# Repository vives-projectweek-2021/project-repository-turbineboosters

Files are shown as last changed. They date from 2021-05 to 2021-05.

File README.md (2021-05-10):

# TurbineBoosters
Welcome to our project repository!

## Choice of motor

To create our windturbine we had to make some choices. The first choice we had to make was wich motor to use as generator.
It soon became clear to us that we had to use a 3 phasse BLDC motor.
We looked around at our options and had 2 motors available, one that generates around 60V:

afbeelding

and another one that generates only around 6V, but has more power:

afbeelding

We decided to go for the motor that generates 60V because we lose 1,4V across the diodes of our 3 phase bridge rectifier and that leaves us with an efficiency of 96%, while the other motor would only offer us an efficiency of about 77%.

## Rectifier + first LoRa module

The power generated by our motor is fed to a 3 phase bridge rectifier.
On this board we measure the current and voltage via a shunt-resistor of 0,5Ω.
The LoRa module (RN2483A) receives this data and sends it peer-to-peer to another LoRa module:

afbeelding

## Lorawan receiver 

The data that we recieve over lorawan on the SODAQ Explorer microconroller is than formated to a byte array. Then the data is send over bluetooth and send to a raspberry pi.

First we wanted to send the data over bluetooth low energy that was on the controller. But the bleutooth HC05 chip doesn't take that much power and is easier to use. 

afbeelding

## Raspberry pi

The data that we receive over bluetooth is than but into an influxdb database. This data is than visualized with the use of grafana.

afbeelding

## Mechanical design

afbeelding

We mounted a bicycle wheel on the shaft of our motor, to which we attached 8 PVC-blades via 3D-printed coupling pieces.

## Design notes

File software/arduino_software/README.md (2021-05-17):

# RN2483_PeerToPeer
 
 This is an example on how to use the RN2483 LoRaWan modem to acheive a secure peer to peer communication.
 
 This library is made for those who have a RN2483 on an existing board. Microchip doesn't advertise the use of peer to peer communication with their RN2483 chips because they were specifically desgined for the LoRaWAN protocol stack. If you are a developer who wants to implement peer to peer communication it is recomended that you directly use the SX12xx lora modems from the start.
 
 This library exploits the limited peer to peer possibilities of the RN2483 to implement secure communication with another RN2483. The connection is stateless so you can broadcast a packet and the device with the correct key and adress will decode and handle the packet.
 
 This library is still in early development. Feel free to add issues or create pull requests if you want to see features added.
 
 planned features:
 * CRC
 * Handshaking
 * Compatibility with other lora modems
 * replay attack prevention
 
 Here is an example sketch:
 
 ```C++
#include "RN2483_P2P.h"

#define loraSerial              Serial2
#define usbSerial               SerialUSB

// Both devices mush have the same AES-key.
const byte key[16] = {0x00, 0x01, 0x02, 0x03, 0x04, 0x05, 0x06, 0x07, 0x08, 0x09, 0x0A, 0x0B, 0x0C, 0x0D, 0x0E, 0x0F};

// set the address of the device where you want te send a packet to
const byte targetAddress[1] = {0x00};

// the adress of this device (The adresses can be the same. It won't loop back)
const byte deviceAddress[1] = {0x00};

RN2483_P2P peerToPeer(usbSerial, loraSerial);

void setup() {

    usbSerial.begin(115200);
    loraSerial.begin(57600);
    loraSerial.setTimeout(1000);
    lora_autobaud();

    usbSerial.println("initializing...");
    
    peerToPeer.initLoRa();
    peerToPeer.setAesKey(key);
    peerToPeer.setAddress(deviceAddress);
}

void loop() 
{
    // uncomment for the transmitter
    //byte payload[10] = {0, 1, 2, 3, 4, 5, 6, 7, 8, 9};
    //peerToPeer.transmitMessage(payload, targetAddress);

    // uncomment for the receiver
    peerToPeer.receiveMessage(handleMessage);
}

void handleMessage(const byte *payload)
{
    // handle the received payload
    
    for (int i=0; i < 10; i++){
        usbSerial.println( (int) payload[i] );
    }
}

void lora_autobaud()
{
    String response = "";
    while (response=="")
    {
        delay(1000);
        loraSerial.write((byte)0x00);
        loraSerial.write(0x55);
        loraSerial.println();
        loraSerial.println("sys get ver");
        response = loraSerial.readStringUntil('\n');
    }
}
 ```
 The code where this library is build upon is [this Code ecample.](https://github.com/jpmeijers/RN2483-Arduino-p2p-examples) <br>
 The encryption library used is [this AES library.](https://github.com/bigfighter/arduino-AES)
 
 This code was tested on a SODAQ ExpLoRer withe an RN2483A with firmware version 1.0.4 but should work on all boards with the RN2483.

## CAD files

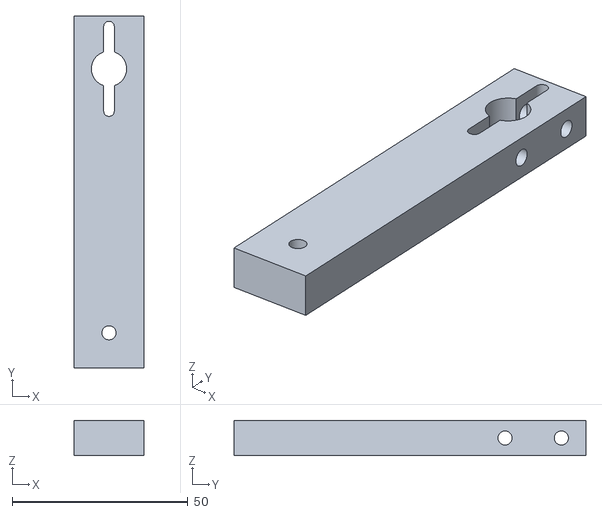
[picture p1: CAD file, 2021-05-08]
hardware/3D_prints/handle.stl
20.0 x 100.0 x 10.0

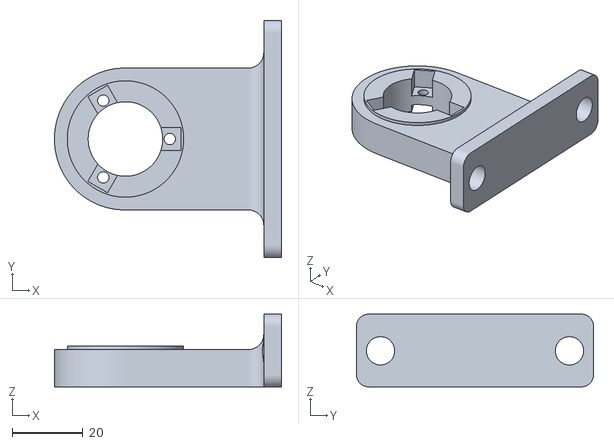
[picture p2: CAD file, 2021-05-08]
hardware/3D_prints/generator_mount.stl
64.0 x 66.9 x 20.5

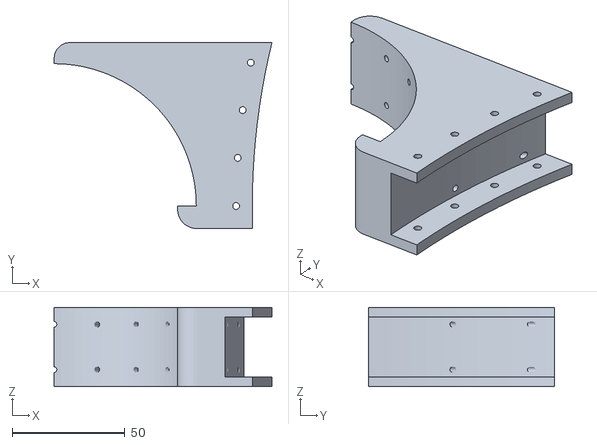
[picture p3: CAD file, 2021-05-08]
hardware/3D_prints/wiek_houder.stl
96.5 x 82.4 x 35.0

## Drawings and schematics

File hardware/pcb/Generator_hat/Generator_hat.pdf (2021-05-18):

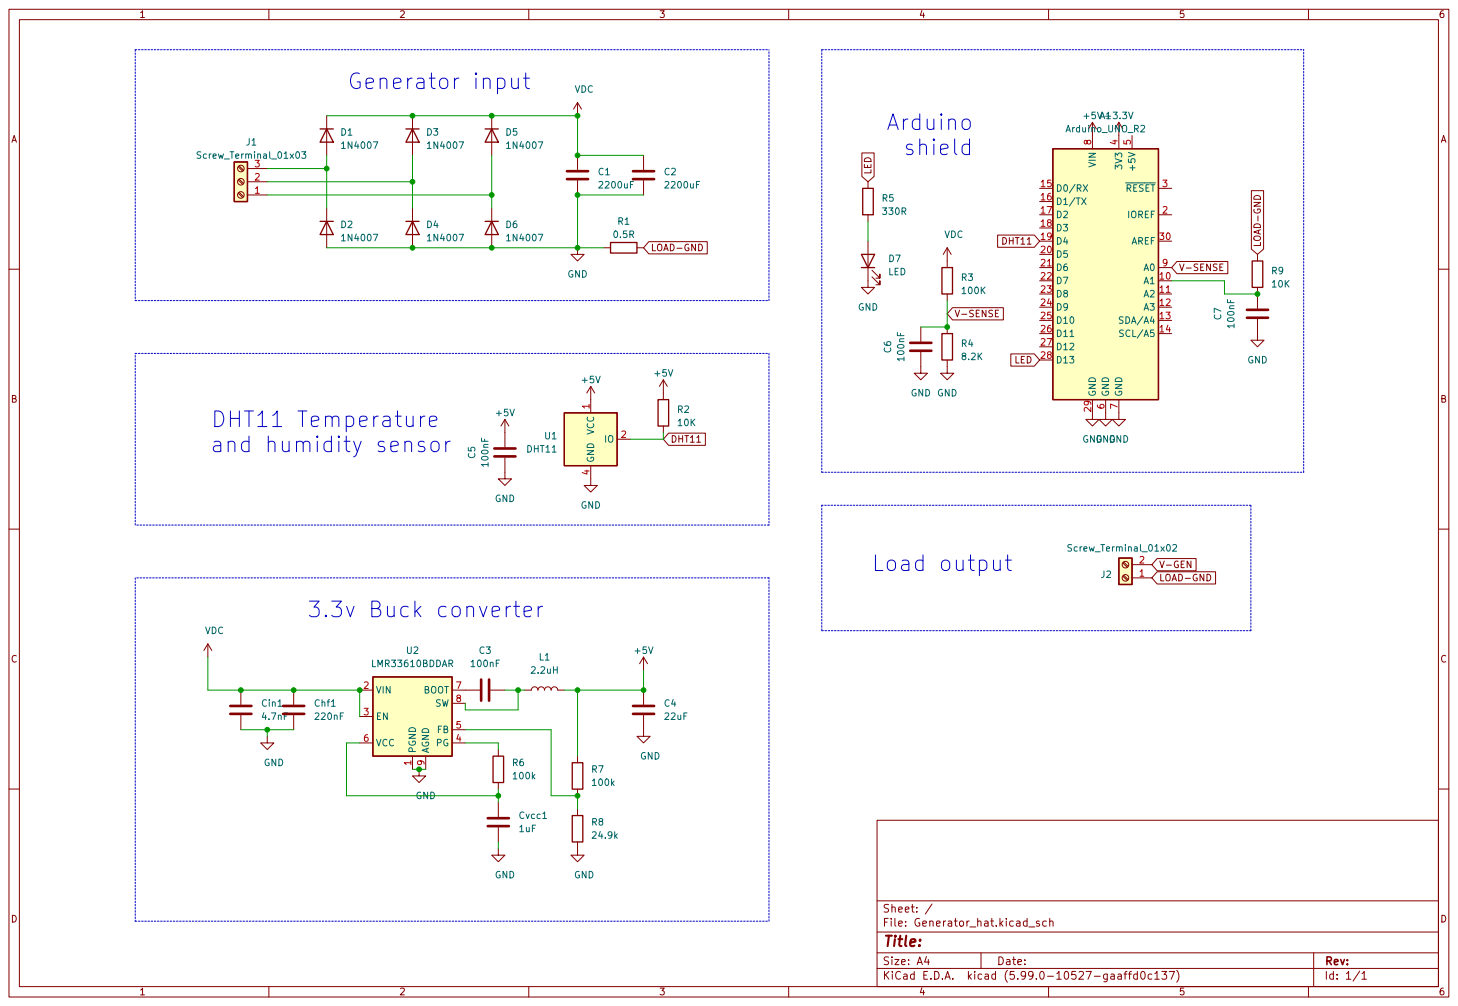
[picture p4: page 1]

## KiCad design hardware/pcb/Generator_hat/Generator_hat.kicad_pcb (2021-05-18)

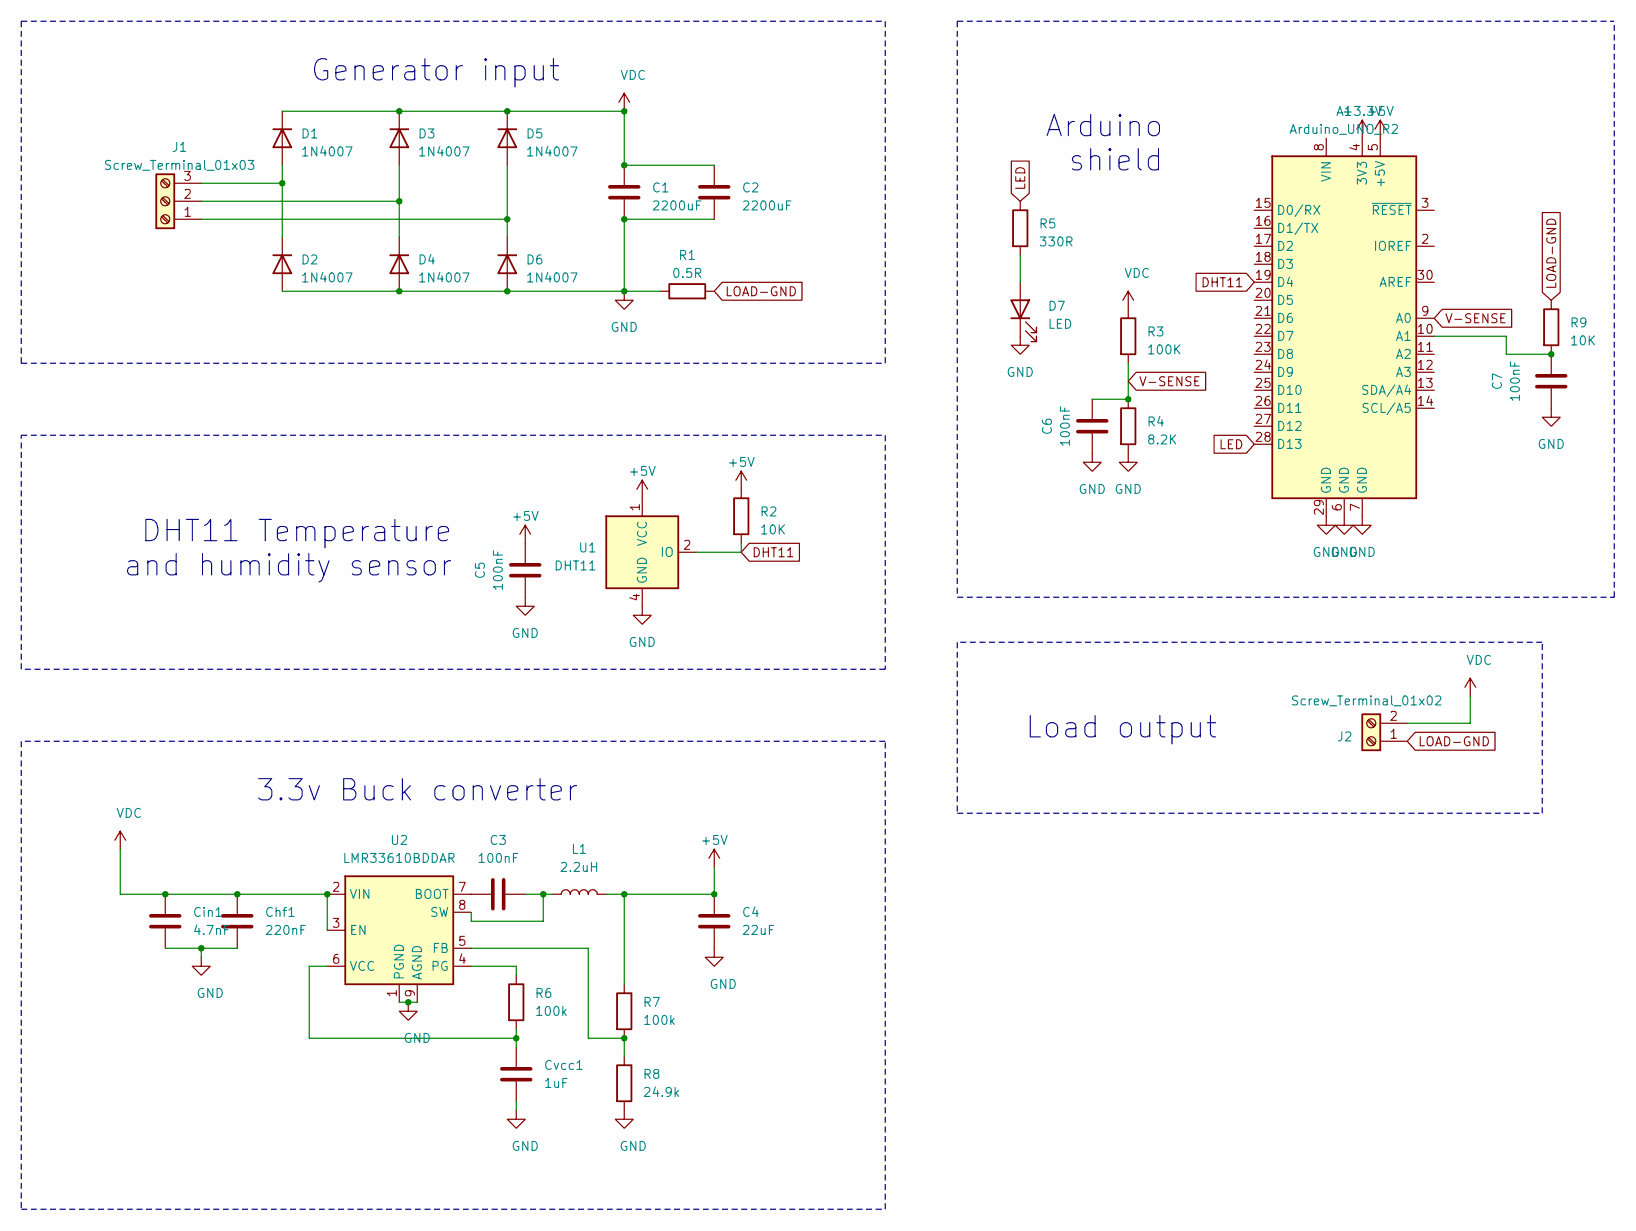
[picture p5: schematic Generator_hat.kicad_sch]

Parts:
A1: Arduino_UNO_R2
C1, C2: 2200uF; CP_Radial_D16.0mm_P7.50mm
C3, C5, C6, C7: 100nF; C_0805_2012Metric_Pad1.18x1.45mm_HandSolder
C4: 22uF; CP_Elec_8x6.9
Chf1: 220nF; C_0805_2012Metric_Pad1.18x1.45mm_HandSolder
Cin1: 4.7nF; C_0805_2012Metric_Pad1.18x1.45mm_HandSolder
Cvcc1: 1uF; C_0805_2012Metric_Pad1.18x1.45mm_HandSolder
D1, D2, D3, D4, D5, D6: 1N4007; D_SMA
D7: LED; LED_D3.0mm
J1: Screw_Terminal_01x03; TerminalBlock_bornier-3_P5.08mm
J2: Screw_Terminal_01x02; TerminalBlock_bornier-2_P5.08mm
L1: 2.2uH; L_Taiyo-Yuden_NR-50xx_HandSoldering
R1: 0.5R; R_Axial_DIN0309_L9.0mm_D3.2mm_P12.70mm_Horizontal
R2, R9: 10K; R_0805_2012Metric_Pad1.20x1.40mm_HandSolder
R3: 100K; R_0805_2012Metric_Pad1.20x1.40mm_HandSolder
R4: 8.2K; R_0805_2012Metric_Pad1.20x1.40mm_HandSolder
R5: 330R; R_0805_2012Metric_Pad1.20x1.40mm_HandSolder
R6, R7: 100k; R_0805_2012Metric_Pad1.20x1.40mm_HandSolder
R8: 24.9k; R_0805_2012Metric_Pad1.20x1.40mm_HandSolder
U1: DHT11; Aosong_DHT11_5.5x12.0_P2.54mm
U2: LMR33610BDDAR; Texas_HSOP-8-1EP_3.9x4.9mm_P1.27mm_ThermalVias

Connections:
+3V3: A1.4 (3V3)
+5V: A1.5 (+5V), C4.1, C5.1, L1.2, R2.1, R7.1, U1.1 (VCC)
DHT11: A1.19 (D4), R2.2, U1.2 (IO)
GND: A1.6 (GND), A1.7 (GND), A1.29 (GND), C1.2, C2.2, C4.2, C5.2, C6.2, C7.2, Chf1.2, Cin1.2, Cvcc1.2, D2.2 (A), D4.2 (A), D6.2 (A), D7.1 (K), R1.1, R4.2, R8.2, U1.4 (GND), U2.1 (PGND), U2.9 (AGND)
LED: A1.28 (D13), R5.1
LOAD-GND: J2.1, R1.2, R9.1
unnamed: A1.10 (A1), C7.1, R9.2
unnamed: C3.1, L1.1, U2.8 (SW)
unnamed: C3.2, U2.7 (BOOT)
unnamed: Cvcc1.1, R6.2, U2.6 (VCC)
unnamed: D1.2 (A), D2.1 (K), J1.3
unnamed: D3.2 (A), D4.1 (K), J1.2
unnamed: D5.2 (A), D6.1 (K), J1.1
unnamed: D7.2 (A), R5.2
unnamed: R6.1, U2.4 (PG)
unnamed: R7.2, R8.1, U2.5 (FB)
V-SENSE: A1.9 (A0), C6.1, R3.2, R4.1
VDC: C1.1, C2.1, Chf1.1, Cin1.1, D1.1 (K), D3.1 (K), D5.1 (K), J2.2, R3.1, U2.2 (VIN), U2.3 (EN)

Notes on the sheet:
DHT11 Temperature and humidity sensor
Generator input
3.3v Buck converter
Arduino shield
Load output

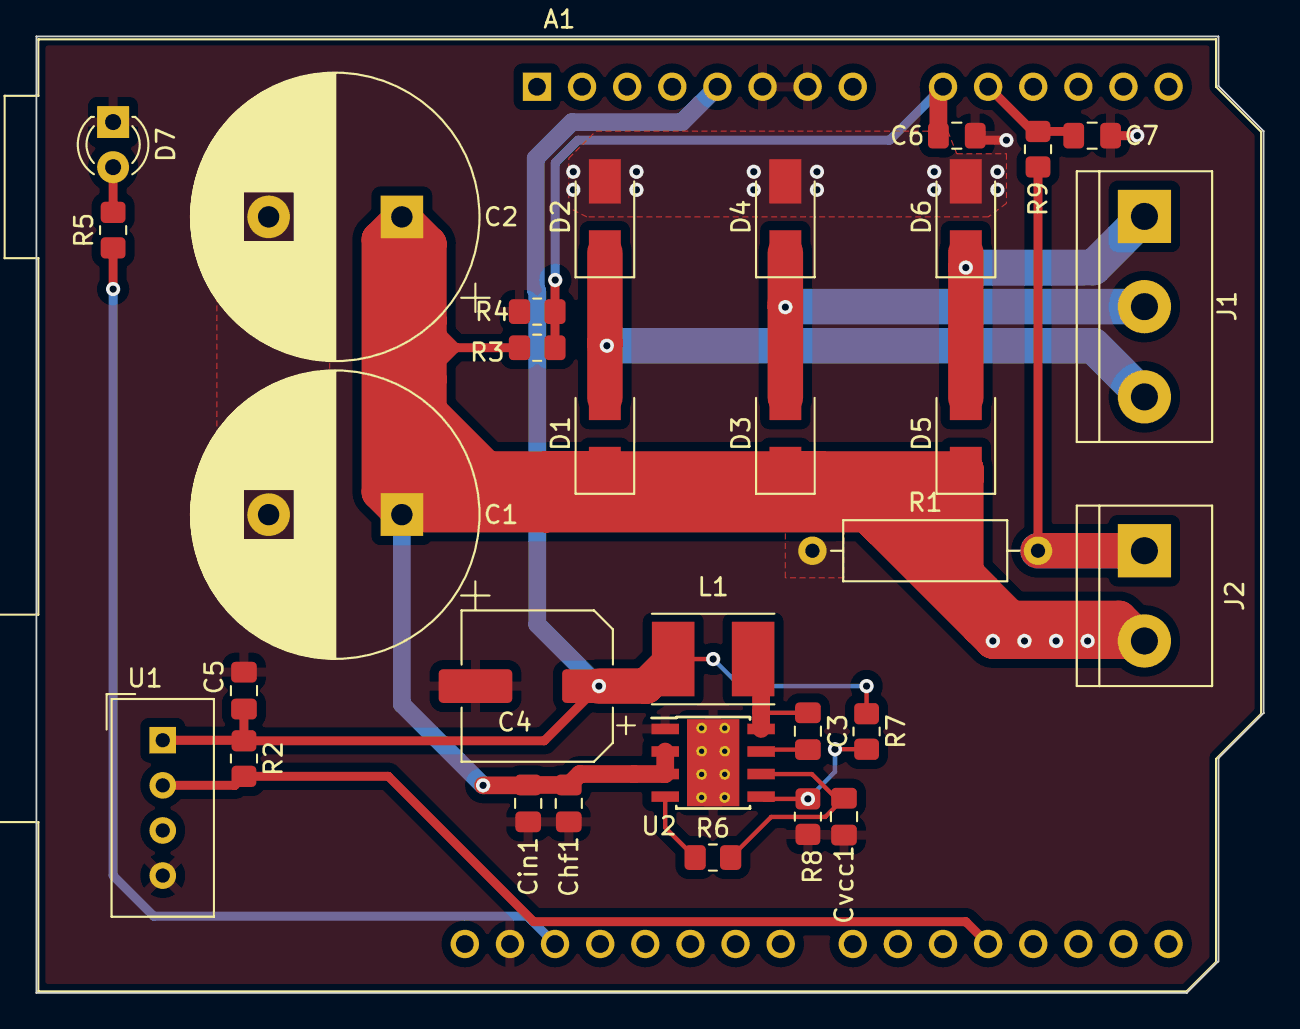
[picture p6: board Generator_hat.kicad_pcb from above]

Board: 2 copper layers, 69.1 x 53.8 mm, 32 parts (0 on the bottom side), 17 nets.

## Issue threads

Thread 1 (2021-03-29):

PCB Board beschrijven

thomascrmbz, 2021-03-29:
Beschrijf wat er allemaal op de pcb moet komen, deel het op in componenten.
Maak ook issues / pull requests aan voor alle componenten (enkel documentatie).
- [ ] ethernet port
- [ ] sensor hat
- [ ] hoog vermogen sensors
- [ ] laag vermogen sensors
- [ ] lcd display
- [ ] batterij
- [ ] outputs (usb, 5V, 12V)
- [x] power convertors (100vac to dc)
- [ ] uitbreiding: rem systeem
- [ ] cm4 connectors
- [x] generator input
- [ ] Microcontroller keuze

Closed 2024-02-22.

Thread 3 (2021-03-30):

Monitoring Stack beschrijven

thomascrmbz, 2021-03-30:
Een sensor hat zal gemaakt worden voor op de 40pin connector van de pi.
InfluxDB zal alle waarden opslaan (1s, 5s of 10s? intervallen)
Met Grafana kunnen we mooie grafieken maken met deze data.
Met een simpele docker-compose kan dit zeer makeelijk gemaakt worden.

Closed 2024-02-22.

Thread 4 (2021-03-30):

Sensoren beschrijven

thomascrmbz, 2021-03-30:
Omdat de sensor hat gecombineerd zal worden met een andere opdracht zitten er al een paar sensoren standaard op.
De extra sensoren moeten nog beslist worden.

thomascrmbz, 2021-04-05:
Standaard sensoren die er al op zitten
- BME sensor (luchtkwaliteit)
- lichtsensor
- 2 drukknoppen
- LCD display
- ADC
- RGB LED
- LED
- Motor driver (kleine motors zoals een ventilator)

DylanMissu, 2021-04-06:
We kunnen er misschien een vibratie sensor op zetten om te weten wanneer de turbine te hard trilt. Moest dat niet kunnen we er een rotatiesnelheid-meter in implementeren en dan de belasting verhogen als het te snel draait.

Closed 2024-02-22.

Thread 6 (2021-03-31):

Metingen motor doen

thomascrmbz, 2021-03-31:

DylanMissu, 2021-03-31:
Na het meten van de motor kwam ik tot de conclusie dat deze ongeschikt is voor onze toepassing, omdat de inductie motor moeilijk te gebruiken is als generator. Als we dit dan toch wilden doen hadden we complexe schakelingen nodig en ging sowiso een slechte efficientie geven. Voor die reden opteren we een driefasige synchroonmotor te gebruiken die we kunnen aankopen of gebruiken van school.

thomascrmbz, 2021-04-02:
Ik denk dat het handig is om een denkbeeldige motor te nemen en specificaties op te stellen, zodat we daarmee ons pcb board kunnen maken en dan later op zoek gaan naar de motor die aan onze vereisten voldoet.

Closed 2024-02-22.

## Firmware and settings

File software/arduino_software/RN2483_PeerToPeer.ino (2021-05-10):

#include <DHT.h>
#include <DHT_U.h>

#include "AES.h"
#include "RN2483_P2P.h"

#define loraSerial              Serial2
#define usbSerial               SerialUSB
#define btSerial                Serial

#define LED_PIN                 9
#define CURRENT_PIN             A1
#define VOLTAGE_PIN             A0

#define DHT11PIN                4
#define DHTTYPE                 DHT11

#define R_SHUNT                 0.5     //Ohms
#define R1                      100000  //Ohms
#define R2                      8200    //Ohms

#define ADC_RESOLUTION          12      //Bits
#define SUPPLY_VOLTAGE          3.3     //Volt
#define SAMPLE_INTERVAL         10     //ms
#define N_SAMPLES               10

// Both devices mush have the same AES-key.
const byte key[16] = {0x00, 0x01, 0x02, 0x03, 0x04, 0x05, 0x06, 0x07, 0x08, 0x09, 0x0A, 0x0B, 0x0C, 0x0D, 0x0E, 0x0F};

// set the address of the device where you want te send a packet to
const byte targetAddress[1] = {0x00};

// the adress of this device (The adresses can be the same. It won't loop back)
const byte deviceAddress[1] = {0x00};

bool ledState = false;
bool stat = true;

DHT dht(DHT11PIN, DHTTYPE);
RN2483_P2P peerToPeer(usbSerial, loraSerial);

void setup() {
    pinMode(VOLTAGE_PIN, INPUT);
    pinMode(CURRENT_PIN, INPUT);
    pinMode(LED_PIN, OUTPUT);
    
    pulse();

    btSerial.begin(9600);
    usbSerial.begin(115200);
    loraSerial.begin(57600);
    loraSerial.setTimeout(1000);
    lora_autobaud();

    usbSerial.println("initializing...");
    
    peerToPeer.initLoRa();
    peerToPeer.setAesKey(key);
    peerToPeer.setAddress(deviceAddress);

    analogReadResolution(ADC_RESOLUTION);

    dht.begin();
}


void loop() 
{
    // uncomment for the transmitter
    transmit(); 

    // uncomment for the receiver
    //peerToPeer.receiveMessage(handleMessage);
}

void printPayload(const byte *payload){
    double humid = ((payload[8]<<8)|(payload[9]))/100.0;
    double temp = ((payload[6]<<8)|(payload[7]))/100.0;
    double volt = ((payload[4]<<8)|(payload[5]))/100.0;
    double amp = ((payload[2]<<8)|(payload[3]))/100.0;
    double power = ((payload[0]<<8)|(payload[1]))/100.0;

    usbSerial.print("Payload: ");
    for (int i=0; i<10; i++){
        usbSerial.print(payload[i] >> 4, HEX);
        usbSerial.print(payload[i] & 0x0f, HEX);
    }
    usbSerial.println();

    usbSerial.print("Temperature: ");
    usbSerial.print(temp);
    usbSerial.println("°C");
    
    usbSerial.print("Humitity: ");
    usbSerial.print(humid);
    usbSerial.println("%");
    
    usbSerial.print("Voltage: ");
    usbSerial.print(volt);
    usbSerial.println("V");
    
    usbSerial.print("Amps: ");
    usbSerial.print(amp);
    usbSerial.println("A");
    
    usbSerial.print("Power: ");
    usbSerial.print(power);
    usbSerial.println("W");

    usbSerial.println();
}

void handleMessage(const byte *payload)
{
    // pulse status led
    pulse();

    // decode the payload into usable values
    double humid = ((payload[8]<<8)|(payload[9]))/100.0;
    double temp = ((payload[6]<<8)|(payload[7]))/100.0;
    double volt = ((payload[4]<<8)|(payload[5]))/100.0;
    double amp = ((payload[2]<<8)|(payload[3]))/100.0;
    double power = ((payload[0]<<8)|(payload[1]))/100.0;

    // Printing payload to btSerial and usbSerial
    usbSerial.print("Payload: ");
    for (int i=0; i < 10; i++){
        btSerial.print(payload[i] >> 4, HEX);
        btSerial.print(payload[i] & 0x0f, HEX);
    }
    
    btSerial.println();

    // print to usb serial
    printPayload(payload);
}

void transmit() {
    byte tempPayload[10] = {0};    

    int sumVolt = 0;
    int sumAmp = 0;
    double sumTemp = 0;
    double sumHumid = 0;
    
    for (int i=0; i<N_SAMPLES; i++) {        
        sumTemp += dht.readTemperature();
        sumHumid += dht.readHumidity();
        sumAmp += analogRead(CURRENT_PIN);
        sumVolt += analogRead(VOLTAGE_PIN);
        delay(SAMPLE_INTERVAL);
    }

    double volt = (sumVolt/N_SAMPLES)*(SUPPLY_VOLTAGE / pow(2,ADC_RESOLUTION))*(1+(R1/R2)); 
    double amp = (sumAmp/N_SAMPLES)*(SUPPLY_VOLTAGE / pow(2,ADC_RESOLUTION))/R_SHUNT;
    double temp = sumTemp/N_SAMPLES;
    double humid = sumHumid/N_SAMPLES;

    // add values to payload for transmission through lora
    tempPayload[0] = (int)(volt*amp*100)>>8;
    tempPayload[1] = (int)(volt*amp*100)&0x00ff;
    
    tempPayload[2] = (int)(amp*100)>>8;
    tempPayload[3] = (int)(amp*100)&0x00ff;
    
    tempPayload[4] = (int)(volt*100)>>8;
    tempPayload[5] = (int)(volt*100)&0x00ff;

    tempPayload[6] = (int)(temp*100)>>8;
    tempPayload[7] = (int)(temp*100)&0x00ff;
    
    tempPayload[8] = (int)(humid*100)>>8;
    tempPayload[9] = (int)(humid*100)&0x00ff;

    usbSerial.println("Decoded: ");
    printPayload(tempPayload);
    usbSerial.println();

    // transmit payload through LoRa
    peerToPeer.transmitMessage(tempPayload, targetAddress);

    // pulse led to display that the data has been sent
    pulse();
}

void lora_autobaud()
{
    String response = "";
    while (response=="")
    {
        delay(1000);
        loraSerial.write((byte)0x00);
        loraSerial.write(0x55);
        loraSerial.println();
        loraSerial.println("sys get ver");
        response = loraSerial.readStringUntil('\n');
    }
}

void pulse()
{
    digitalWrite(LED_PIN, HIGH);
    delay(50);
    digitalWrite(LED_PIN, LOW);
}

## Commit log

2021-04-02 added kicad project with basic ac to dc convertion schematic
    [DC_Converter.kicad_pcb, DC_Converter.kicad_sch]
2021-04-02 added voltage and current sensing to schematic
    [DC_Converter.kicad_sch]
2021-04-05 Added gitignore for future kicad backups
2021-04-05 Added sensor-hat pcb
    [sensor-hat.kicad_pcb, sensor-hat.kicad_sch]
2021-05-01 added Arduino software submodule
2021-05-07 added gif to powerpoint
2021-05-08 added 3d printed parts and blender project
    [generator_mount.stl, handle.stl, wiek_houder.stl]
2021-05-08 added pcb and schematic
    [DC_Converter.kicad_pcb, DC_Converter.kicad_sch, Generator_hat.kicad_pcb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]
2021-05-10 updated ppt
    [Generator_hat.kicad_pcb, Generator_hat.kicad_sch]
2021-05-10 updated arduino code
2021-05-18 update pcb
    [Generator_hat.kicad_pcb, Generator_hat.kicad_sch]
